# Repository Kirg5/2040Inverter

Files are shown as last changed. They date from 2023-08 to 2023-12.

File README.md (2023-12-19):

# 2040Inverter
 RP2040 Based BLDC Inverter for sensored motors, capable of putting out 50a 100v, for use in high power ebike/escooter applications.
 
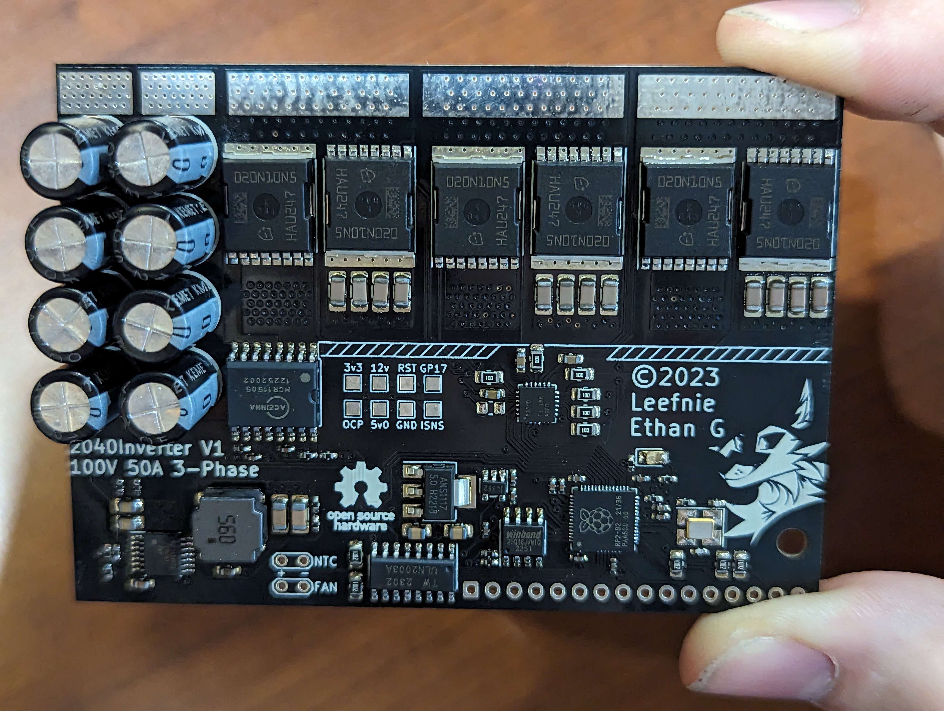
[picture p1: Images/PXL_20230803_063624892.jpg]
Inverter PCB

## Usage
This is a standalone motor inverter, and not a complete motor controller. It does not contain any inputs for assist sensors or throttles as these are sent to the inverter over UART by a seperate MCU, located in the display. You can find the files for the display [here](https://github.com/Kirg5/RP2040-ILI9488-HUD). 

Upon power-up, the fan will breifly be set to full speed, the brake light will turn white, and 6 tones from 1khz to 6khz will be played as part of the self test sequence. If less than 6 tones play it indicates an issue sending power to each of the motor phases and the inverter will throw itself into an error state. Error states can also be thrown if an issue is detected with any of the sensors (current sensor, voltage sensor, either temperature sensor, or motor encoder)

The inverter shall recieve a throttle input from the MCU in the display over uart with a range of 0-255. These values correlate to the current that the inverter will attempt to draw from the battery, ranging from 0 to the maximum set forward current as defined in the firmware. The maximum forward current should never be set higher than 50A with this inverter (30A without active cooling). The throttle does not directly control duty cycle, and instead the duty cycle is controlled through a PID loop that will match the current draw to the requested current. This PID system will work at low speeds, but as the motor EMF approaches the battery voltage at high speeds, the ability to continue to feed current into the motor will fall off. When the PID loop can no longer provide the requested current to the motor (when Dutycycle<sub>PID</sub> > Dutycycle<sub>throttle</sub>), it will smoothly switch to using the direct value from the throttle instead of the PID controlled value.

This inverter supports regenerative braking, where the kinetic energy that would normally be lost to heat while decellerating gets converted into electrical energy to charge the battery. It works in a very similar fashion to the forward power control where a regen signal with a value ranging from 0-255 is sent from the display MCU to the inverter, and it uses a pid loop to map these values to a range of 0 to the maximum reverse current defined in the firmware. The maximum reverse current should be set to the maximum charge current of your BMS, or the maximum charge current of your cells multipled by the number of parallel groups, whichever is lower. You should never set the maximum reverse current value higher than 50a even if your battery can handle it as the current sensor on the inverter cannot measure currents this high, and it can cause damage to the PCB and it's components, especially if you are not using active cooling.

## Wiring 
Wiring the inverter is fairly straightforward; there are 5 large power pads along the top edge and a 16 pin JST connector along the bottom edge, and 2 sets of labelled through holes for the thermistor and the fan.
### The 5 power pads as ordered from left to right are:
1. +VCC (abs. max 100V)
2. GND
3. Phase A (Blue Phase)
4. Phase B (Green Phase)
5. Phase C (Yellow Phase)

### The 16 pins on the JST connector in numerical order are:
1.  LedR    (For brake light, active low)
2.  LedG    (For brake light, active low)
3.  LedB    (For brake light, active low)
4.  RlyCTL  (Output to main relay MOSFET/BJT)
5.  PWR_OK  (Signal from display MCU that precharging has finished and it is ok to power on)
6.  BOOTSEL (RP2040 bootsel button, for firmware flashing)
7.  +12v    (12v 500mA output)
8.  +5v     (5v 500mA output)
9.  USB_DP  (To USB port)
10. USB_DM  (To USB port)
11. UartTX  (To display)
12. UartRX  (To display)
13. HallC   (Blue hall line, active low)
14. HallB   (Green hall line, active low)
15. HallA   (Yellow hall line, active low)
16. GND

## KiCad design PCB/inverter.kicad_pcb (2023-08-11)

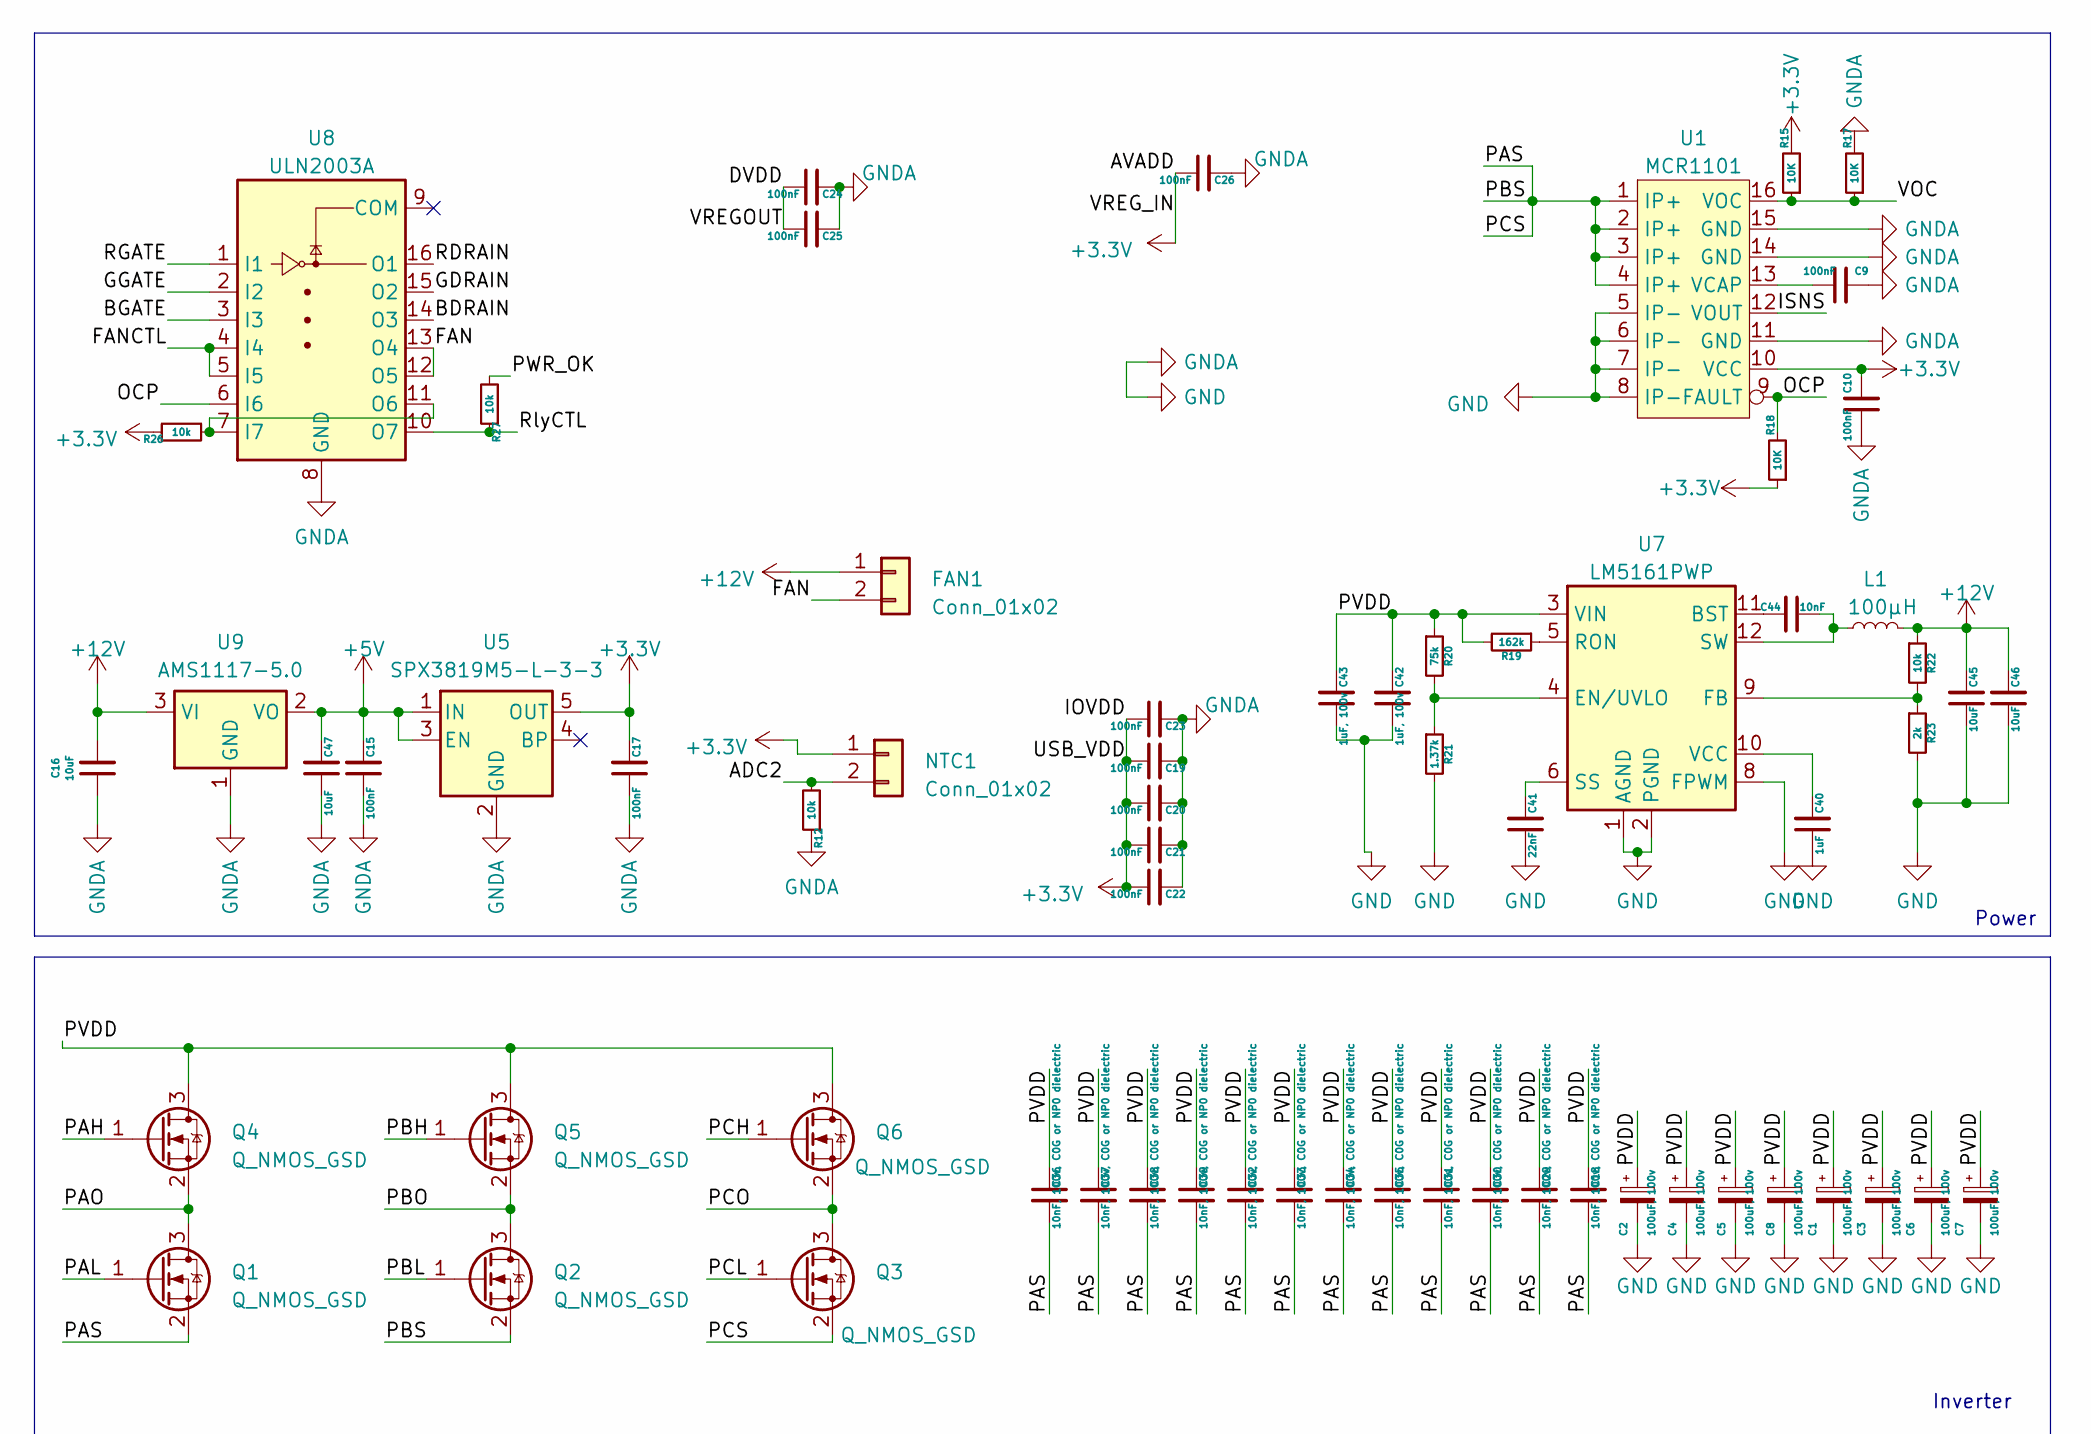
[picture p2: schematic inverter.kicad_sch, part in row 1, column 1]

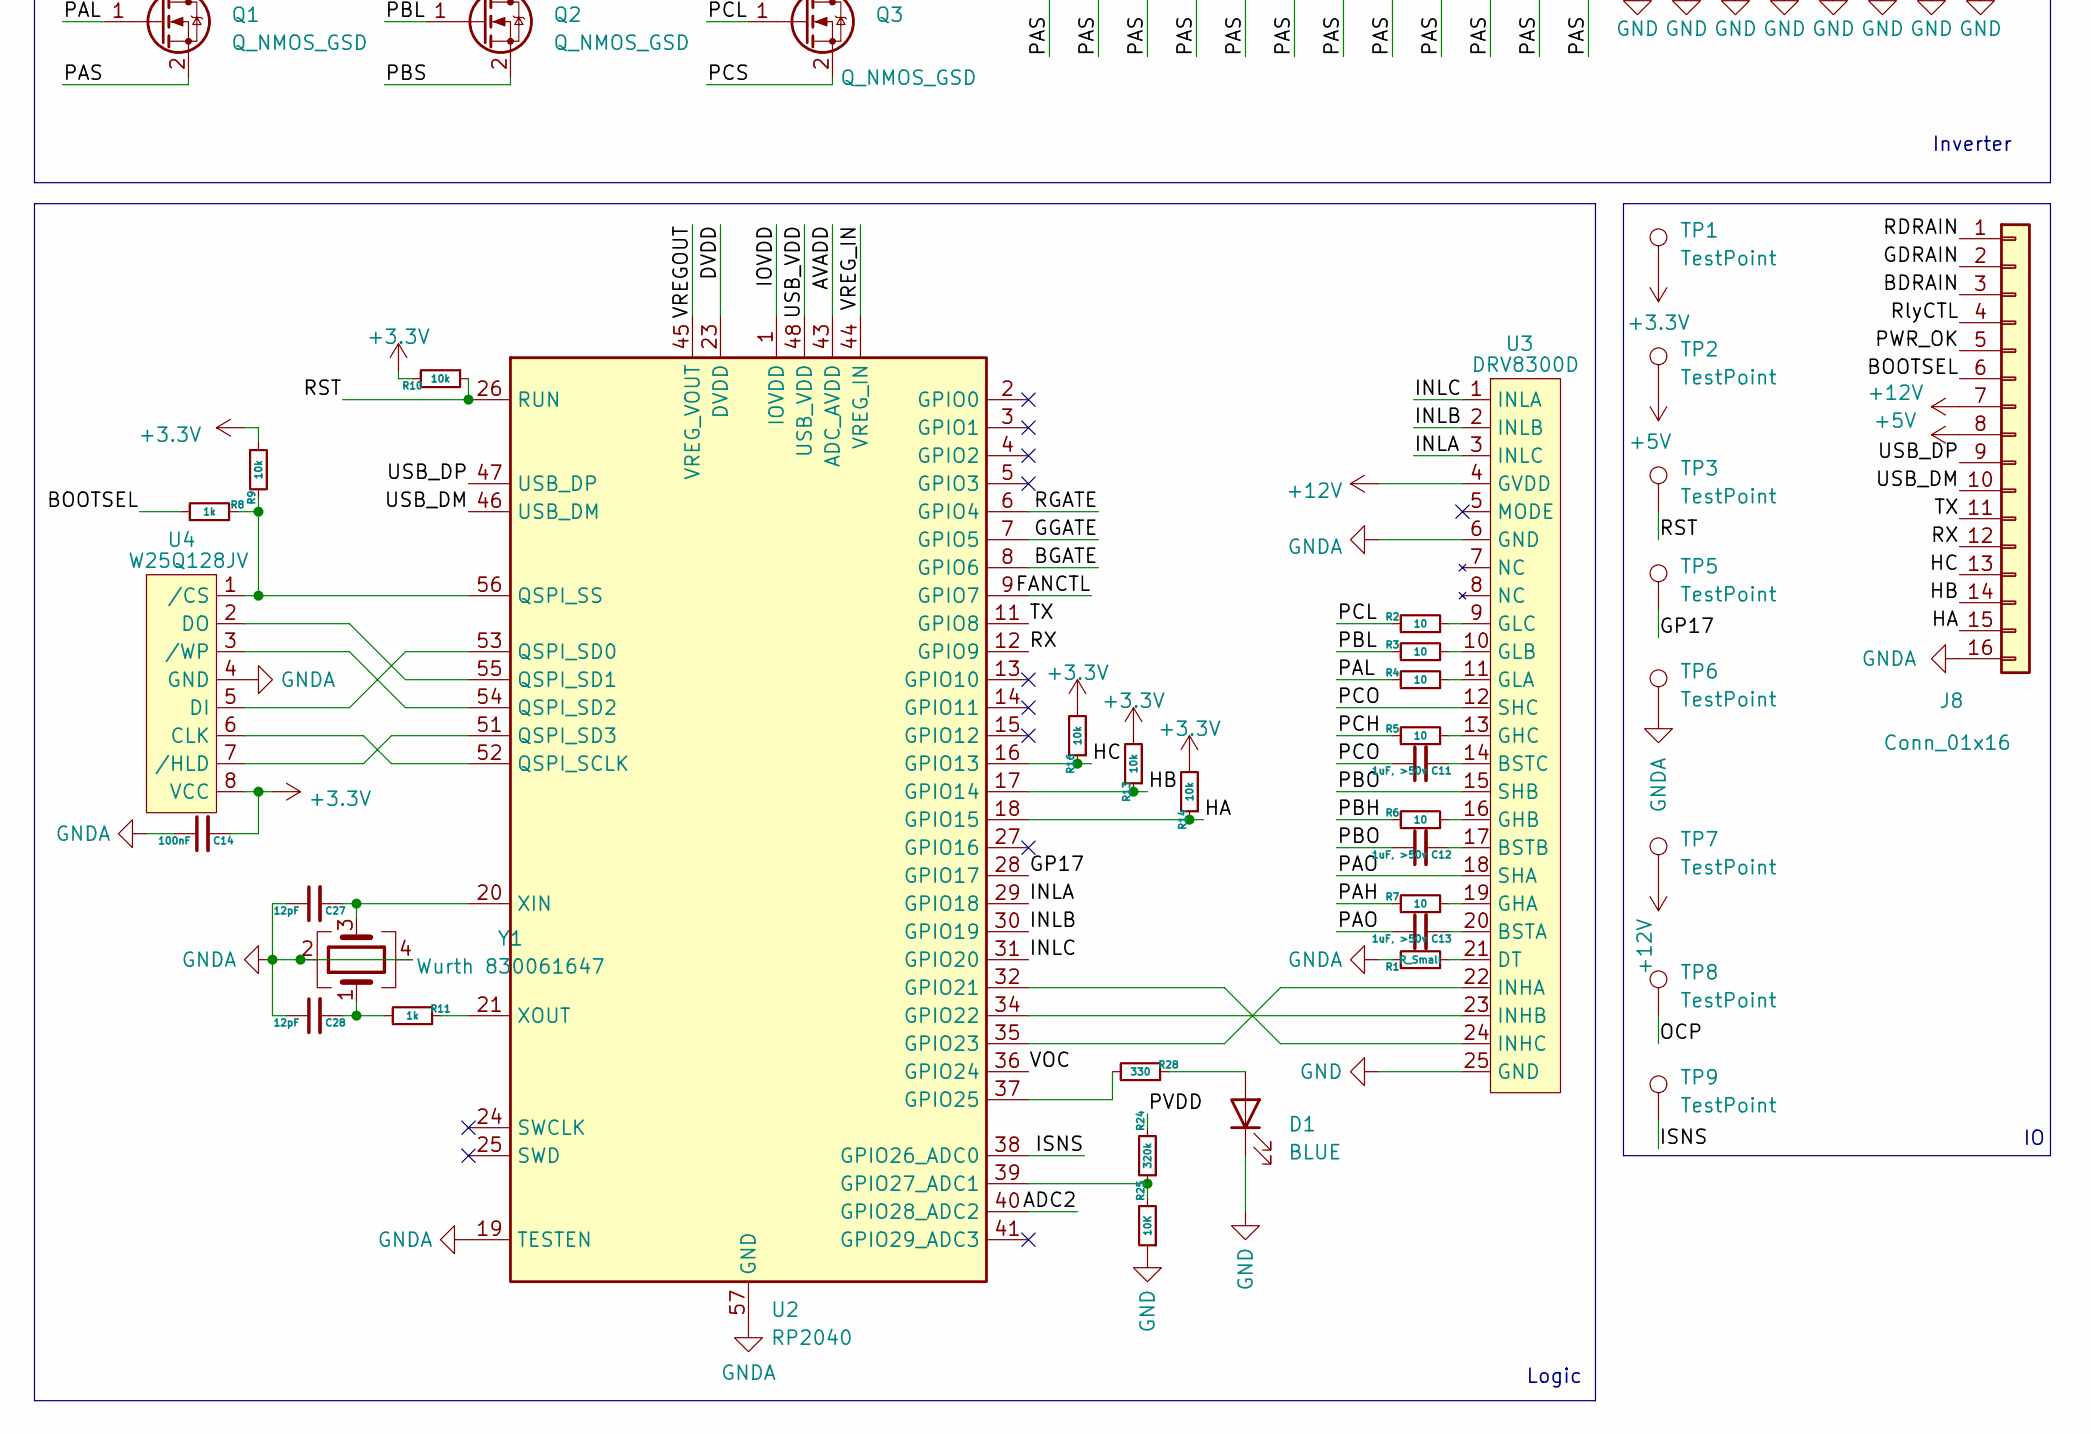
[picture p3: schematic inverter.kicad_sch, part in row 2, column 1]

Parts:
C1, C2, C3, C4, C5, C6, C7, C8: 100uF, 100v; CP_Radial_D8.0mm_P3.50mm
C9, C10, C14, C15, C17, C19, C20, C21, C22, C23, C24, C25, C26: 100nF; C_0402_1005Metric_Pad0.74x0.62mm_HandSolder
C11, C12, C13: 1uF, >50v; C_0603_1608Metric_Pad1.08x0.95mm_HandSolder
C16, C47: 10uF; C_0805_2012Metric_Pad1.18x1.45mm_HandSolder
C18, C29, C30, C31, C32, C33, C34, C35, C36, C37, C38, C39: 10nF, 100v, C0G or NP0 dielectric; C_1206_3216Metric_Pad1.33x1.80mm_HandSolder
C27, C28: 12pF; C_0402_1005Metric_Pad0.74x0.62mm_HandSolder
C40: 1uF; C_0603_1608Metric_Pad1.08x0.95mm_HandSolder
C41: 22nF; C_0603_1608Metric_Pad1.08x0.95mm_HandSolder
C42, C43: 1uF, 100v; C_0805_2012Metric_Pad1.18x1.45mm_HandSolder
C44: 10nF; C_0603_1608Metric_Pad1.08x0.95mm_HandSolder
C45, C46: 10uF; C_1206_3216Metric_Pad1.33x1.80mm_HandSolder
D1: BLUE; LED_0805_2012Metric_Pad1.15x1.40mm_HandSolder
FAN1: Conn_01x02; TestPoint_2Pads_Pitch2.54mm_Drill0.8mm
J8: Conn_01x16; JST_XH_B16B-XH-A_1x16_P2.50mm_Vertical
L1: 100µH; Wurth 74404084560
NTC1: Conn_01x02; TestPoint_2Pads_Pitch2.54mm_Drill0.8mm
Q1, Q2, Q3, Q4, Q5, Q6: Q_NMOS_GSD; Infineon_PG-HSOF-8-1
R1: R_Small; R_0805_2012Metric_Pad1.20x1.40mm_HandSolder
R2, R3, R4, R5, R6, R7: 10; R_0805_2012Metric_Pad1.20x1.40mm_HandSolder
R8, R11: 1k; R_0402_1005Metric_Pad0.72x0.64mm_HandSolder
R9, R10, R12, R22: 10k; R_0402_1005Metric_Pad0.72x0.64mm_HandSolder
R13, R14, R16, R26, R27: 10k; R_0805_2012Metric_Pad1.20x1.40mm_HandSolder
R15, R17, R18, R25: 10K; R_0402_1005Metric_Pad0.72x0.64mm_HandSolder
R19: 162k; R_0402_1005Metric_Pad0.72x0.64mm_HandSolder
R20: 75k; R_0402_1005Metric_Pad0.72x0.64mm_HandSolder
R21: 1.37k; R_0402_1005Metric_Pad0.72x0.64mm_HandSolder
R23: 2k; R_0402_1005Metric_Pad0.72x0.64mm_HandSolder
R24: 320k; R_0402_1005Metric_Pad0.72x0.64mm_HandSolder
R28: 330; R_0402_1005Metric_Pad0.72x0.64mm_HandSolder
TP1, TP2, TP3, TP5, TP6, TP7, TP8, TP9: TestPoint; TestPoint_Pad_1.5x1.5mm
U1: MCR1101; SOIC-16W_7.5x10.3mm_P1.27mm
U2: RP2040; QFN-56-1EP_7x7mm_P0.4mm_EP3.2x3.2mm
U3: DRV8300D; VQFN-24-1EP_4x4mm_P0.5mm_EP2.5x2.5mm
U4: W25Q128JV; SOIC-8-1EP_3.9x4.9mm_P1.27mm_EP2.29x3mm
U5: SPX3819M5-L-3-3; SOT-23-5
U7: LM5161PWP; HTSSOP-14-1EP_4.4x5mm_P0.65mm_EP3.4x5mm_Mask3x3.1mm
U8: ULN2003A; SOIC-16_3.9x9.9mm_P1.27mm
U9: AMS1117-5.0; SOT-223-3_TabPin2
Y1: Wurth 830061647; Crystal_SMD_3225-4Pin_3.2x2.5mm_HandSoldering

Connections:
+3.3V: C10.2, C14.2, C17.2, C19.1, C20.1, C21.1, C22.1, C23.1, C26.1, NTC1.1, R9.1, R10.2, R13.2, R14.2, R15.2, R16.2, R18.1, R26.1, TP1.1, U1.10 (VCC), U2.1 (IOVDD), U2.10 (IOVDD), U2.22 (IOVDD), U2.33 (IOVDD), U2.42 (IOVDD), U2.43 (ADC_AVDD), U2.44 (VREG_IN), U2.48 (USB_VDD), U2.49 (IOVDD), U4.8 (VCC), U5.5 (OUT); also elsewhere on the board
+5V: C15.2, C47.2, J8.8, TP2.1, U5.1 (IN), U5.3 (EN), U9.2 (VO)
+12V: C16.2, C45.2, C46.2, FAN1.1, J8.7, L1.2, R22.1, TP7.1, U3.4 (GVDD), U9.3 (VI); also elsewhere on the board
/ADC2: NTC1.2, R12.2, U2.40 (GPIO28_ADC2); also elsewhere on the board
/BDRAIN: J8.3, U8.14 (O3)
/BGATE: U2.8 (GPIO6), U8.3 (I3)
/BOOTSEL: J8.6, R8.1
/DVDD: C24.1, C25.1, U2.23 (DVDD), U2.45 (VREG_VOUT), U2.50 (DVDD)
/FAN: FAN1.2, U8.12 (O5), U8.13 (O4); also elsewhere on the board
/FANCTL: U2.9 (GPIO7), U8.4 (I4), U8.5 (I5)
/GDRAIN: J8.2, U8.15 (O2)
/GGATE: U2.7 (GPIO5), U8.2 (I2)
/GP17: TP5.1, U2.28 (GPIO17)
/HA: J8.15, R14.1, U2.18 (GPIO15)
/HB: J8.14, R13.1, U2.17 (GPIO14)
/HC: J8.13, R16.1, U2.16 (GPIO13)
/INLA: U2.29 (GPIO18), U3.3 (INLC)
/INLB: U2.30 (GPIO19), U3.2 (INLB)
/INLC: U2.31 (GPIO20), U3.1 (INLA)
/ISNS: TP9.1, U1.12 (VOUT), U2.38 (GPIO26_ADC0)
/OCP: R18.2, TP8.1, U1.9 (FAULT), U8.6 (I6)
/PAH: Q4.1 (G), R7.1
/PAL: Q1.1 (G), R4.1
/PAO: C13.1, Q1.3 (D), Q4.2 (S), U3.18 (SHA)
/PAS: C18.2, C29.2, C30.2, C31.2, C32.2, C33.2, C34.2, C35.2, C36.2, C37.2, C38.2, C39.2, Q1.2 (S), Q2.2 (S), Q3.2 (S), U1.1 (IP+), U1.2 (IP+), U1.3 (IP+), U1.4 (IP+)
/PBH: Q5.1 (G), R6.1
/PBL: Q2.1 (G), R3.1
/PBO: C12.1, Q2.3 (D), Q5.2 (S), U3.15 (SHB)
/PCH: Q6.1 (G), R5.1
/PCL: Q3.1 (G), R2.1
/PCO: C11.1, Q3.3 (D), Q6.2 (S), U3.12 (SHC)
/PVDD: C1.1, C2.1, C3.1, C4.1, C5.1, C6.1, C7.1, C8.1, C18.1, C29.1, C30.1, C31.1, C32.1, C33.1, C34.1, C35.1, C36.1, C37.1, C38.1, C39.1, C42.2, C43.2, Q4.3 (D), Q5.3 (D), Q6.3 (D), R19.2, R20.1, R24.2, U7.3 (VIN)
/PWR_OK: J8.5, R27.2
/RDRAIN: J8.1, U8.16 (O1)
/RGATE: U2.6 (GPIO4), U8.1 (I1)
/RST: R10.1, TP3.1, U2.26 (RUN)
/RX: J8.12, U2.12 (GPIO9)
/RlyCTL: J8.4, R27.1, U8.10 (O7)
/TX: J8.11, U2.11 (GPIO8)
/USB_DM: J8.10, U2.46 (USB_DM)
/USB_DP: J8.9, U2.47 (USB_DP)
/VOC: R15.1, R17.1, U1.16 (VOC), U2.36 (GPIO24)
GND: C1.2, C2.2, C3.2, C4.2, C5.2, C6.2, C7.2, C8.2, C9.2, C10.1, C14.1, C15.1, C16.1, C17.1, C19.2, C20.2, C21.2, C22.2, C23.2, C24.2, C25.2, C26.2, C27.1, C28.1, C40.1, C41.1, C42.1, C43.1, C45.1, C46.1, C47.1, D1.1 (K), J8.16, R1.1, R12.1, R17.2, R21.2, R23.2, R25.1, TP6.1, U1.5 (IP-), U1.6 (IP-), U1.7 (IP-), U1.8 (IP-), U1.11 (GND), U1.14 (GND), U1.15 (GND), U2.19 (TESTEN), U2.57 (GND), U3.6 (GND), U3.25 (GND), U4.4 (GND), U5.2 (GND), U7.1 (AGND), U7.2 (PGND), U7.8 (FPWM), U7.15 (AGND), U8.8 (GND), U9.1 (GND), Y1.2, Y1.4
unnamed: C28.2, R11.1, Y1.1
unnamed: C44.1, L1.1, U7.12 (SW), U7.13 (SW)
unnamed: D1.2 (A), R28.1
unnamed: C9.1, U1.13 (VCAP)
unnamed: U2.32 (GPIO21), U3.24 (INHC)
unnamed: U2.34 (GPIO22), U3.23 (INHB)
unnamed: U2.35 (GPIO23), U3.22 (INHA)
unnamed: R28.2, U2.37 (GPIO25)
unnamed: R24.1, R25.2, U2.39 (GPIO27_ADC1)
unnamed: U2.52 (QSPI_SCLK), U4.6 (CLK)
unnamed: U2.53 (QSPI_SD0), U4.5 (DI)
unnamed: U2.55 (QSPI_SD1), U4.2 (DO)
unnamed: U2.54 (QSPI_SD2), U4.3 (/WP)
unnamed: U2.51 (QSPI_SD3), U4.7 (/HLD)
unnamed: R8.2, R9.2, U2.56 (QSPI_SS), U4.1 (/CS)
unnamed: C27.2, U2.20 (XIN), Y1.3
unnamed: R11.2, U2.21 (XOUT)
unnamed: C13.2, U3.20 (BSTA)
unnamed: C12.2, U3.17 (BSTB)
unnamed: C11.2, U3.14 (BSTC)
unnamed: R1.2, U3.21 (DT)
unnamed: R7.2, U3.19 (GHA)
unnamed: R6.2, U3.16 (GHB)
unnamed: R5.2, U3.13 (GHC)
unnamed: R4.2, U3.11 (GLA)
unnamed: R3.2, U3.10 (GLB)
unnamed: R2.2, U3.9 (GLC)
unnamed: C44.2, U7.11 (BST)
unnamed: R20.2, R21.1, U7.4 (EN/UVLO)
unnamed: R22.2, R23.1, U7.9 (FB)
unnamed: R19.1, U7.5 (RON)
unnamed: C41.2, U7.6 (SS)
unnamed: C40.2, U7.10 (VCC)
unnamed: R26.2, U8.7 (I7), U8.11 (O6)

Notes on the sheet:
Inverter
Power
Logic

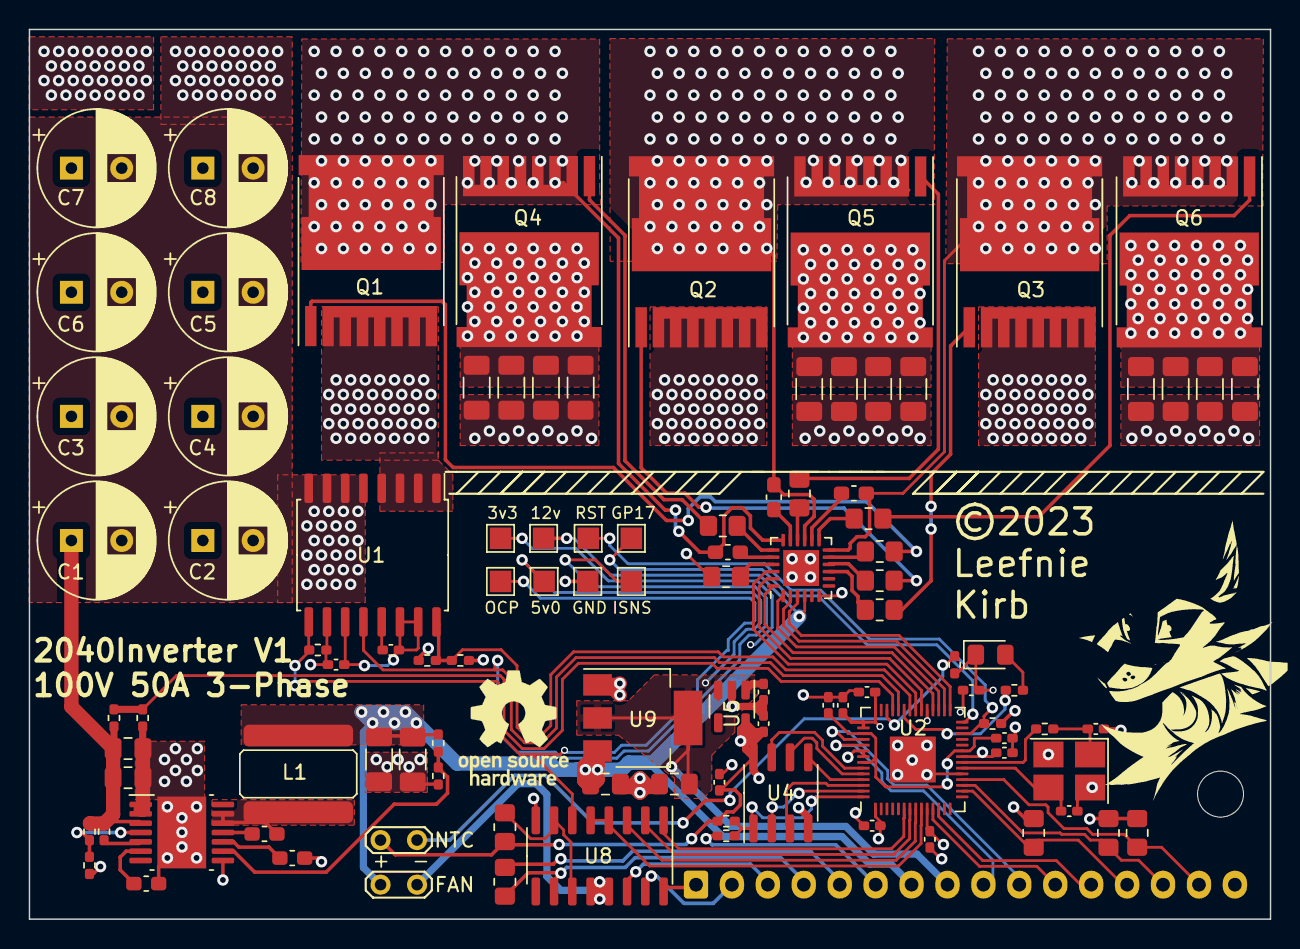
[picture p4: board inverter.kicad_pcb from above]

Board: 4 copper layers, 86.4 x 61.9 mm, 103 parts (1 on the bottom side), 77 nets.

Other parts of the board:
FAN: Conn_01x02; TestPoint_2Pads_Pitch2.54mm_Drill0.8mm
NTC: Conn_01x02; TestPoint_2Pads_Pitch2.54mm_Drill0.8mm

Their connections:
+3.3V: NTC.1; also elsewhere on the board
+12V: FAN.1; also elsewhere on the board
/ADC2: NTC.2; also elsewhere on the board
/FAN: FAN.2; also elsewhere on the board

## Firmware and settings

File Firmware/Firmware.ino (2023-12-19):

#include <RP2040_PWM.h>
#include "Sine.h"
#include "Notes.h"

RP2040_PWM* PWM_Instance[6];

  // Config Vars
  int wheelSize = 26;                 //Wheel diameter in inches
  int polePairs = 42;                 //Motor pole pair count
  int maxForwardCurrent = 50;         //Maximum acceleration current
  int maxReverseCurrent = 10;         //Maximum regen braking current
  int seriesPairs = 20;               //Battery series pairs 
  int undervoltageThreshold = 15;     //Hard undervoltage cutoff to prevent mosfet underdriving
  uint32_t refenFreqSwitching = 1000; //Static PWM frequency for regen braking
  uint32_t freqSwitching = 2000;      //Static PWM frequency for acceleration
  
  // MOSFET pins
  const int phaseAGateLowPin = 20;
  const int phaseBGateLowPin = 19;
  const int phaseCGateLowPin = 18;
  const int phaseAGateHighPin = 23;
  const int phaseBGateHighPin = 22;
  const int phaseCGateHighPin = 21;
  
  // Hall sensor pins
  const int hallSensorAPin = 13;
  const int hallSensorBPin = 14;
  const int hallSensorCPin = 15;

  // ADC pins
  const int currentSensePin = 26;
  const int voltageSensePin = 27;
  const int tempSensePin = 28;
  const int ambientTempSensePin = 29;

  // Misc pins
  const int ledR = 4;
  const int ledG = 5;
  const int ledB = 6;
  const int Fan = 7;
  const int OCP_Int = 24;

  // System Vars
  int currentAngle = 0;
  int estimatedAngle = 0;
  int lastAngle = 0;
  int voltageRaw = 0;
  int currentRaw = 0;
  float voltage = 0;
  float current = 0;
  float phaseCurrent = 0;
  float speed = 0;
  float RotationRate = 0;
  float acceleration = 0;
  float jerk = 0;
  unsigned long timer = 0;
  int phaseTime0 = 0;
  int phaseTime1 = 0;
  int phaseTime2 = 0;
  unsigned long period = 0;
  int dutyCycle = 60;
  int reverseDutyCycle = 0;
  int pulseCount = 0;
  uint32_t freqSwitchingDyn = 0;
  int PWMMode = 0; 
    //PWMMode 0 = Power-on test
    //PWMMode 1 = Square wave, static frequency
    //PWMMode 2 = Square wave, dynamic frequency
    //PWMMode 3 = Sine wave, static frequency
    //PWMMode 4 = Sine wave, dynamic frequency
    //PWMMode 5 = Multi pulse synchronous sine
    //PWMMode 6 = Square wave tone

  void setup() {
  analogWrite(Fan, 255);

  // LED pins
  pinMode(LED_BUILTIN, OUTPUT);
  pinMode(ledR, OUTPUT);
  pinMode(ledG, OUTPUT);
  pinMode(ledB, OUTPUT);

  //Initialize High Side PWM Channels
  PWM_Instance[1] = new RP2040_PWM(phaseAGateHighPin, freqSwitching, 0);
  PWM_Instance[2] = new RP2040_PWM(phaseBGateHighPin, freqSwitching, 0);
  PWM_Instance[3] = new RP2040_PWM(phaseCGateHighPin, freqSwitching, 0);

  //Initialize Low Side PWM Channels
  PWM_Instance[4] = new RP2040_PWM(phaseAGateLowPin, freqSwitching, 0);
  PWM_Instance[5] = new RP2040_PWM(phaseBGateLowPin, freqSwitching, 0);
  PWM_Instance[6] = new RP2040_PWM(phaseCGateLowPin, freqSwitching, 0);

  // Set the pins as inputs for hall effect sensors
  pinMode(hallSensorAPin, INPUT);
  pinMode(hallSensorBPin, INPUT);
  pinMode(hallSensorCPin, INPUT);

  // Setup ADC
  pinMode(currentSensePin, INPUT);
  pinMode(voltageSensePin, INPUT);
  pinMode(tempSensePin, INPUT);
  pinMode(ambientTempSensePin, INPUT);

  // Initialize serial
  Serial.begin(9600);

  delay(100);
  analogWrite(Fan, 0);
}

void loop() 
  {
  // Read raw current and voltage values
  int currentRaw = analogRead(currentSensePin);
  int voltageRaw = analogRead(voltageSensePin);

  // Calculate actual voltage and current
  current = (currentRaw - 511.5) * 50 / 511.5;
  voltage = voltageRaw * 108.9 / 1023;

  //Calculate phase current
  //phaseCurrent = (current * (255 / dutyCycle));

  // Read hall sensors
  int hallSensorAState = digitalRead(hallSensorAPin);
  int hallSensorBState = digitalRead(hallSensorBPin);
  int hallSensorCState = digitalRead(hallSensorCPin);

  // Calculate electrical angle
         if (hallSensorAState == HIGH && hallSensorBState == LOW && hallSensorCState == HIGH) {
    currentAngle = 0;
    timer = micros();
  } else if (hallSensorAState == HIGH && hallSensorBState == LOW && hallSensorCState == LOW) {
    currentAngle = 60;
  } else if (hallSensorAState == HIGH && hallSensorBState == HIGH && hallSensorCState == LOW) {
    currentAngle = 120;
    period = (micros() - timer);
  } else if (hallSensorAState == LOW && hallSensorBState == HIGH && hallSensorCState == LOW) {
    currentAngle = 180;
  } else if (hallSensorAState == LOW && hallSensorBState == HIGH && hallSensorCState == HIGH) {
    currentAngle = 240;
  } else if (hallSensorAState == LOW && hallSensorBState == LOW && hallSensorCState == HIGH) {
    currentAngle = 300;
  }

  //Braking
  //if (reverseDutyCycle > 0) {
    //analogWrite(ledR, 255);
    //Regen control loop here
  //} else {
    //analogWrite(ledR, 0);
  //}

  //Derivatives calculation
  //if (lastAngle != currentAngle) {
    //int phaseTime2 = phaseTime1;
    //int phaseTime1 = (millis() - phaseTime0);
    //int lastAngle = currentAngle;
    //int phaseTime0 = millis();
 // }
  //add the shit for slope and exponent here

  //Calculate RPM
  //RotationRate = (60000/period/polePairs);

  //Calculate Speed from RPM
  //speed = (RotationRate * wheelSize * 0.00479);

  //Placeholder dynamic frequency eqn
  //freqSwitchingDyn = ((RotationRate * 0.1) + 2000);
      if (period > 12000) {
      freqSwitchingDyn = 1500; 
  } else if (period > 8000 && period < 11999) {
      freqSwitchingDyn = 2000; 
    } else if (period > 6000 && period < 7999) {
      freqSwitchingDyn = 3000; 
    } else if (period > 4000 && period < 5999) {
freqSwitchingDyn = 4000; 
      } else if (period > 2000 && period < 3999) {
freqSwitchingDyn = 5000; 
        } else if (period < 1999) {
freqSwitchingDyn = 8000; 
        }

  //Motor commutation
    if (PWMMode == 1) { // Square wave, static frequency
    if (currentAngle == 0) {
      //High Side
      PWM_Instance[1]->setPWM(phaseAGateHighPin, freqSwitching, dutyCycle);
      PWM_Instance[2]->setPWM(phaseBGateHighPin, freqSwitching, 0);
      PWM_Instance[3]->setPWM(phaseCGateHighPin, freqSwitching, 0);
      //Low Side
      PWM_Instance[4]->setPWM(phaseAGateLowPin, freqSwitching, 0);
      PWM_Instance[5]->setPWM(phaseBGateLowPin, freqSwitching, dutyCycle);
      PWM_Instance[6]->setPWM(phaseCGateLowPin, freqSwitching, 0);
    } else if (currentAngle == 60) {
      //High Side
      PWM_Instance[1]->setPWM(phaseAGateHighPin, freqSwitching, dutyCycle);
      PWM_Instance[2]->setPWM(phaseBGateHighPin, freqSwitching, 0);
      PWM_Instance[3]->setPWM(phaseCGateHighPin, freqSwitching, 0);
      //Low Side
      PWM_Instance[4]->setPWM(phaseAGateLowPin, freqSwitching, 0);
      PWM_Instance[5]->setPWM(phaseBGateLowPin, freqSwitching, 0);
      PWM_Instance[6]->setPWM(phaseCGateLowPin, freqSwitching, dutyCycle);
    } else if (currentAngle == 120) {
      //High Side
      PWM_Instance[1]->setPWM(phaseAGateHighPin, freqSwitching, 0);
      PWM_Instance[2]->setPWM(phaseBGateHighPin, freqSwitching, dutyCycle);
      PWM_Instance[3]->setPWM(phaseCGateHighPin, freqSwitching, 0);
      //Low Side
      PWM_Instance[4]->setPWM(phaseAGateLowPin, freqSwitching, 0);
      PWM_Instance[5]->setPWM(phaseBGateLowPin, freqSwitching, 0);
      PWM_Instance[6]->setPWM(phaseCGateLowPin, freqSwitching, dutyCycle);
    } else if (currentAngle == 180) {
      //High Side
      PWM_Instance[1]->setPWM(phaseAGateHighPin, freqSwitching, 0);
      PWM_Instance[2]->setPWM(phaseBGateHighPin, freqSwitching, dutyCycle);
      PWM_Instance[3]->setPWM(phaseCGateHighPin, freqSwitching, 0);
      //Low Side
      PWM_Instance[4]->setPWM(phaseAGateLowPin, freqSwitching, dutyCycle);
      PWM_Instance[5]->setPWM(phaseBGateLowPin, freqSwitching, 0);
      PWM_Instance[6]->setPWM(phaseCGateLowPin, freqSwitching, 0);
    } else if (currentAngle == 240) {
      //High Side
      PWM_Instance[1]->setPWM(phaseAGateHighPin, freqSwitching, 0);
      PWM_Instance[2]->setPWM(phaseBGateHighPin, freqSwitching, 0);
      PWM_Instance[3]->setPWM(phaseCGateHighPin, freqSwitching, dutyCycle);
      //Low Side
      PWM_Instance[4]->setPWM(phaseAGateLowPin, freqSwitching, dutyCycle);
      PWM_Instance[5]->setPWM(phaseBGateLowPin, freqSwitching, 0);
      PWM_Instance[6]->setPWM(phaseCGateLowPin, freqSwitching, 0);
    } else if (currentAngle == 300) {
      //High Side
      PWM_Instance[1]->setPWM(phaseAGateHighPin, freqSwitching, 0);
      PWM_Instance[2]->setPWM(phaseBGateHighPin, freqSwitching, 0);
      PWM_Instance[3]->setPWM(phaseCGateHighPin, freqSwitching, dutyCycle);
      //Low Side
      PWM_Instance[4]->setPWM(phaseAGateLowPin, freqSwitching, 0);
      PWM_Instance[5]->setPWM(phaseBGateLowPin, freqSwitching, dutyCycle);
      PWM_Instance[6]->setPWM(phaseCGateLowPin, freqSwitching, 0);
    }
  } else if (PWMMode == 2) { // Square wave, dynamic frequency
    if (currentAngle == 0) {
      //High Side
      PWM_Instance[1]->setPWM(phaseAGateHighPin, freqSwitchingDyn, dutyCycle);
      PWM_Instance[2]->setPWM(phaseBGateHighPin, freqSwitchingDyn, 0);
      PWM_Instance[3]->setPWM(phaseCGateHighPin, freqSwitchingDyn, 0);
      //Low Side
      PWM_Instance[4]->setPWM(phaseAGateLowPin, freqSwitchingDyn, 0);
      PWM_Instance[5]->setPWM(phaseBGateLowPin, freqSwitchingDyn, dutyCycle);
      PWM_Instance[6]->setPWM(phaseCGateLowPin, freqSwitchingDyn, 0);
    } else if (currentAngle == 60) {
      //High Side
      PWM_Instance[1]->setPWM(phaseAGateHighPin, freqSwitchingDyn, dutyCycle);
      PWM_Instance[2]->setPWM(phaseBGateHighPin, freqSwitchingDyn, 0);
      PWM_Instance[3]->setPWM(phaseCGateHighPin, freqSwitchingDyn, 0);
      //Low Side
      PWM_Instance[4]->setPWM(phaseAGateLowPin, freqSwitchingDyn, 0);
      PWM_Instance[5]->setPWM(phaseBGateLowPin, freqSwitchingDyn, 0);
      PWM_Instance[6]->setPWM(phaseCGateLowPin, freqSwitchingDyn, dutyCycle);
    } else if (currentAngle == 120) {
      //High Side
      PWM_Instance[1]->setPWM(phaseAGateHighPin, freqSwitchingDyn, 0);
      PWM_Instance[2]->setPWM(phaseBGateHighPin, freqSwitchingDyn, dutyCycle);
      PWM_Instance[3]->setPWM(phaseCGateHighPin, freqSwitchingDyn, 0);
      //Low Side
      PWM_Instance[4]->setPWM(phaseAGateLowPin, freqSwitchingDyn, 0);
      PWM_Instance[5]->setPWM(phaseBGateLowPin, freqSwitchingDyn, 0);
      PWM_Instance[6]->setPWM(phaseCGateLowPin, freqSwitchingDyn, dutyCycle);
    } else if (currentAngle == 180) {
      //High Side
      PWM_Instance[1]->setPWM(phaseAGateHighPin, freqSwitchingDyn, 0);
      PWM_Instance[2]->setPWM(phaseBGateHighPin, freqSwitchingDyn, dutyCycle);
      PWM_Instance[3]->setPWM(phaseCGateHighPin, freqSwitchingDyn, 0);
      //Low Side
      PWM_Instance[4]->setPWM(phaseAGateLowPin, freqSwitchingDyn, dutyCycle);
      PWM_Instance[5]->setPWM(phaseBGateLowPin, freqSwitchingDyn, 0);
      PWM_Instance[6]->setPWM(phaseCGateLowPin, freqSwitchingDyn, 0);
    } else if (currentAngle == 240) {
      //High Side
      PWM_Instance[1]->setPWM(phaseAGateHighPin, freqSwitchingDyn, 0);
      PWM_Instance[2]->setPWM(phaseBGateHighPin, freqSwitchingDyn, 0);
      PWM_Instance[3]->setPWM(phaseCGateHighPin, freqSwitchingDyn, dutyCycle);
      //Low Side
      PWM_Instance[4]->setPWM(phaseAGateLowPin, freqSwitchingDyn, dutyCycle);
      PWM_Instance[5]->setPWM(phaseBGateLowPin, freqSwitchingDyn, 0);
      PWM_Instance[6]->setPWM(phaseCGateLowPin, freqSwitchingDyn, 0);
    } else if (currentAngle == 300) {
      //High Side
      PWM_Instance[1]->setPWM(phaseAGateHighPin, freqSwitchingDyn, 0);
      PWM_Instance[2]->setPWM(phaseBGateHighPin, freqSwitchingDyn, 0);
      PWM_Instance[3]->setPWM(phaseCGateHighPin, freqSwitchingDyn, dutyCycle);
      //Low Side
      PWM_Instance[4]->setPWM(phaseAGateLowPin, freqSwitchingDyn, 0);
      PWM_Instance[5]->setPWM(phaseBGateLowPin, freqSwitchingDyn, dutyCycle);
      PWM_Instance[6]->setPWM(phaseCGateLowPin, freqSwitchingDyn, 0);
    }
  } else if (PWMMode == 3) { // Sine wave, static frequency
      //int estimatedAngle = (currentAngle + (phaseTime1 * idk));
  } else if (PWMMode == 4) { // Sine wave, dynamic frequency

  } else if (PWMMode == 5) { // Multi pulse synchronous sine

  } else if (PWMMode == 6) { // Square wave tone

  } else if (PWMMode == 0) { // Test
      //High Side
      PWM_Instance[1]->setPWM(phaseAGateHighPin, 1000, 10);
      PWM_Instance[2]->setPWM(phaseBGateHighPin, 1000, 0);
      PWM_Instance[3]->setPWM(phaseCGateHighPin, 1000, 0);
      //Low Side
      PWM_Instance[4]->setPWM(phaseAGateLowPin, 1000, 0);
      PWM_Instance[5]->setPWM(phaseBGateLowPin, 1000, 10);
      PWM_Instance[6]->setPWM(phaseCGateLowPin, 1000, 0);
    delay(100);
      //High Side
      PWM_Instance[1]->setPWM(phaseAGateHighPin, 2000, 10);
      PWM_Instance[2]->setPWM(phaseBGateHighPin, 2000, 0);
      PWM_Instance[3]->setPWM(phaseCGateHighPin, 2000, 0);
      //Low Side
      PWM_Instance[4]->setPWM(phaseAGateLowPin, 2000, 0);
      PWM_Instance[5]->setPWM(phaseBGateLowPin, 2000, 0);
      PWM_Instance[6]->setPWM(phaseCGateLowPin, 2000, 10);
    delay(100);
      //High Side
      PWM_Instance[1]->setPWM(phaseAGateHighPin, 3000, 0);
      PWM_Instance[2]->setPWM(phaseBGateHighPin, 3000, 10);
      PWM_Instance[3]->setPWM(phaseCGateHighPin, 3000, 0);
      //Low Side
      PWM_Instance[4]->setPWM(phaseAGateLowPin, 3000, 0);
      PWM_Instance[5]->setPWM(phaseBGateLowPin, 3000, 0);
      PWM_Instance[6]->setPWM(phaseCGateLowPin, 3000, 10);
    delay(100);
      //High Side
      PWM_Instance[1]->setPWM(phaseAGateHighPin, 4000, 0);
      PWM_Instance[2]->setPWM(phaseBGateHighPin, 4000, 10);
      PWM_Instance[3]->setPWM(phaseCGateHighPin, 4000, 0);
      //Low Side
      PWM_Instance[4]->setPWM(phaseAGateLowPin, 4000, 10);
      PWM_Instance[5]->setPWM(phaseBGateLowPin, 4000, 0);
      PWM_Instance[6]->setPWM(phaseCGateLowPin, 4000, 0);
    delay(100);
      //High Side
      PWM_Instance[1]->setPWM(phaseAGateHighPin, 5000, 0);
      PWM_Instance[2]->setPWM(phaseBGateHighPin, 5000, 0);
      PWM_Instance[3]->setPWM(phaseCGateHighPin, 5000, 10);
      //Low Side
      PWM_Instance[4]->setPWM(phaseAGateLowPin, 5000, 10);
      PWM_Instance[5]->setPWM(phaseBGateLowPin, 5000, 0);
      PWM_Instance[6]->setPWM(phaseCGateLowPin, 5000, 0);
    delay(100);
      //High Side
      PWM_Instance[1]->setPWM(phaseAGateHighPin, 6000, 0);
      PWM_Instance[2]->setPWM(phaseBGateHighPin, 6000, 0);
      PWM_Instance[3]->setPWM(phaseCGateHighPin, 6000, 10);
      //Low Side
      PWM_Instance[4]->setPWM(phaseAGateLowPin, 6000, 0);
      PWM_Instance[5]->setPWM(phaseBGateLowPin, 6000, 10);
      PWM_Instance[6]->setPWM(phaseCGateLowPin, 6000, 0);
      delay(100);
    PWMMode = 2; 
  }
if (Serial.available() > 0) {
  dutyCycle = 100;
}

analogWrite(LED_BUILTIN, dutyCycle);

Serial.print("angle = ");
Serial.print(currentAngle);
Serial.print("\t Period = ");
Serial.print(period);
Serial.print("\t Frequency = ");
Serial.print(freqSwitchingDyn);
Serial.print("\t RPM = ");
Serial.print(RotationRate);
Serial.print("\t voltage = ");
Serial.print(voltage);
Serial.print("\t current = ");
Serial.println(current);
  delay(0);
}

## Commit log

2023-08-11 Create repository
    [inverter.kicad_pcb, inverter.kicad_sch]
2023-10-21 Fix incorrect PWM frequency
    [Firmware.ino]
2023-11-18 Fix incorrect low side pin numbers
    [Firmware.ino]
2023-11-20 Update README.md
    Fix incorrect hall sensor wiring
2023-12-19 Implement wheel speed sensing and adaptive PWM frequency

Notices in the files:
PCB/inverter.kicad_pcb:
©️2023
